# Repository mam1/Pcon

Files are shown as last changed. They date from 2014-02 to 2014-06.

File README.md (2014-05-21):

###Pcon - multi channel programmable controller
- - - - - - - - - 
#####Tag v0.1-e is the currnet production code, it has been running for six months in 2 instalations. The fsmtng branch is the active development branch.  It is under construction and is not stable.
- - - - - - - - -
The state of up to 8 channels can be controlled by time of day, time of day and a sensor value or manually. Each channel has it onwn schedules.  There can be different schedules for each day of the week. The user interface is a serial terminal command line, the command processor fuctions are detailed below. 

The code was developed in c using SimpleIDE. The development platform is a Parallax C3 making use of flash memory and the SD card.  A DS3231 real time clock module is connected to the C3's i2c bus (pins 28,29) to provide a time reference. The DS3231 module, the AQY212GH relays and terminals for the external connections are mounted on an additional board connected to the C3.

The application can be configured to drive 1 to 8 channels using the preprocessor variable *_NUMBER_OF_CHANNELS* in Pcon.h.  It can be configured to drive IO pins or to drive the Parallax Digital IO Board serial interface. The the preprocessor variable *_DRIVEN* in Pcon.h controls which interface is used. In one implementation I am driving AQY212GH PhotoMOS relays connected to 5 propeller IO pins.  The PhotoMOS relays are rated at 60 V AC/DC 1.1 A. These relays come in a 4-pin DIP package.  They work great to control 24 V zone valves. The second instance is driving a Parallax Digital IO board which can control 8, 120 VAC 8 A loads and accept input from 8 sensors. 
####Language:
C - Propgcc, SimpleIDE, Sublime Text
####Hardware:
* C3 micro controller, Parallax  
* Digital IO Board (DIOB), Sharp solid state relays part# S202S02F, Parallax 
* ChronoDot real time clock module, based on a DS3231, adafruit 
* AQY212GH PhotoMOS relays, Newark
* MID400 AC Line Monitor, Newark 

####Command processor functions:
* name channels  
* manually control channel state  
* set channel control mode (manual, time, time & sensor)
* zero on time time for a channel
* load/save channel information to SD card  
* create and maintain schedules for each channel
* copy and paste schedules between days across channels
* load/save schedules to SD card (default file names)
* load/save schedules to a named file on the SD card
* display current time and date
* set date and time
* display schedules
* display system configuration information
* stop and start the control cogs
* set the real time clock
* reboot from EEPROM

####Command processor commands:
######schedule mode commands:
&nbsp;&nbsp;&nbsp;&nbsp;&nbsp;&nbsp;**copy** - copy the schedule for a channel and day to a buffer<br />
&nbsp;&nbsp;&nbsp;&nbsp;&nbsp;&nbsp;**paste** - paste the buffered schedule into a channel and day<br />
&nbsp;&nbsp;&nbsp;&nbsp;&nbsp;&nbsp;**delete** - delete the schedule for the channel and day<br />
&nbsp;&nbsp;&nbsp;&nbsp;&nbsp;&nbsp;**save** - save edited schedules data to default file<br />
&nbsp;&nbsp;&nbsp;&nbsp;&nbsp;&nbsp;**load** - load schedules from default file<br />
&nbsp;&nbsp;&nbsp;&nbsp;&nbsp;&nbsp;**file {file name} {load|save}** - save or load a named schedule file<br />
&nbsp;&nbsp;&nbsp;&nbsp;&nbsp;&nbsp;**edit** - edit the schedule for a specific channel and day<br />
&nbsp;&nbsp;&nbsp;&nbsp;&nbsp;&nbsp;&nbsp;&nbsp;&nbsp;&nbsp;&nbsp;&nbsp;&nbsp;&nbsp;&nbsp;&nbsp;**delete** - delete a schedule record for the specified time<br />
&nbsp;&nbsp;&nbsp;&nbsp;&nbsp;&nbsp;&nbsp;&nbsp;&nbsp;&nbsp;&nbsp;&nbsp;&nbsp;&nbsp;&nbsp;&nbsp;**on** - set the schedule state to on for the specified time<br />
&nbsp;&nbsp;&nbsp;&nbsp;&nbsp;&nbsp;&nbsp;&nbsp;&nbsp;&nbsp;&nbsp;&nbsp;&nbsp;&nbsp;&nbsp;&nbsp;**off** - set the schedule state to off for the specified time<br />
&nbsp;&nbsp;&nbsp;&nbsp;&nbsp;&nbsp;&nbsp;&nbsp;&nbsp;&nbsp;&nbsp;&nbsp;&nbsp;&nbsp;&nbsp;&nbsp;**quit** - exit schedule edit mode<br />           
######channel mode commands:
&nbsp;&nbsp;&nbsp;&nbsp;&nbsp;&nbsp;**save** - save current channel data to default file<br />
&nbsp;&nbsp;&nbsp;&nbsp;&nbsp;&nbsp;**load** - load channel data from default file<br />
&nbsp;&nbsp;&nbsp;&nbsp;&nbsp;&nbsp;**name** - set the name of a channel<br />
&nbsp;&nbsp;&nbsp;&nbsp;&nbsp;&nbsp;**mode** - set the control mode of a channel, 0-manual, 1-time, 2-time & sensor<br />
&nbsp;&nbsp;&nbsp;&nbsp;&nbsp;&nbsp;**zero {channel #}** - set the on time accumlator for a channel to 0<br />
&nbsp;&nbsp;&nbsp;&nbsp;&nbsp;&nbsp;**on {channel #}** - force the control mode of a channel to manual and set the state to on<br />
&nbsp;&nbsp;&nbsp;&nbsp;&nbsp;&nbsp;**off {channel #}** - force the control mode of a channel to manual and set the state to off<br />
######system commands:
&nbsp;&nbsp;&nbsp;&nbsp;&nbsp;&nbsp;**system** - display system information<br />
&nbsp;&nbsp;&nbsp;&nbsp;&nbsp;&nbsp;**status** - display a formated dump of schedules, channel information and current state for all channels for all days<br />
&nbsp;&nbsp;&nbsp;&nbsp;&nbsp;&nbsp;**time** - display current time and date<br />
&nbsp;&nbsp;&nbsp;&nbsp;&nbsp;&nbsp;**set {YYYY}{MM}{DD}{N(day #)}{HH}{MM}{SS}** - set the real time clock<br />
&nbsp;&nbsp;&nbsp;&nbsp;&nbsp;&nbsp;**shutdown** - force all channels to manual control and turn them off, stop control cogs<br />
&nbsp;&nbsp;&nbsp;&nbsp;&nbsp;&nbsp;**start** - start control cogs<br />
&nbsp;&nbsp;&nbsp;&nbsp;&nbsp;&nbsp;**reboot** - reboot the system from EEPROM<br />
&nbsp;&nbsp;&nbsp;&nbsp;&nbsp;&nbsp;**help(?)** - display list of valid commands<br />

Because the command processor is implemented by a state machine there is a lot of flexibility in the way tokens can be entered.  Entering a '?' will display the current state of the command fsm and a list of commands and tokens (INT for a integer and STR for a quoted string) that are valid in that state. ESC will clear input buffers and reset the state machines.   Tokens can be entered individually or strung together. Spaces, commas, colons and slashes will work as a delimiters. If the fsm requires additional information a prompt will be displayed, however the main loop will not wait for input.

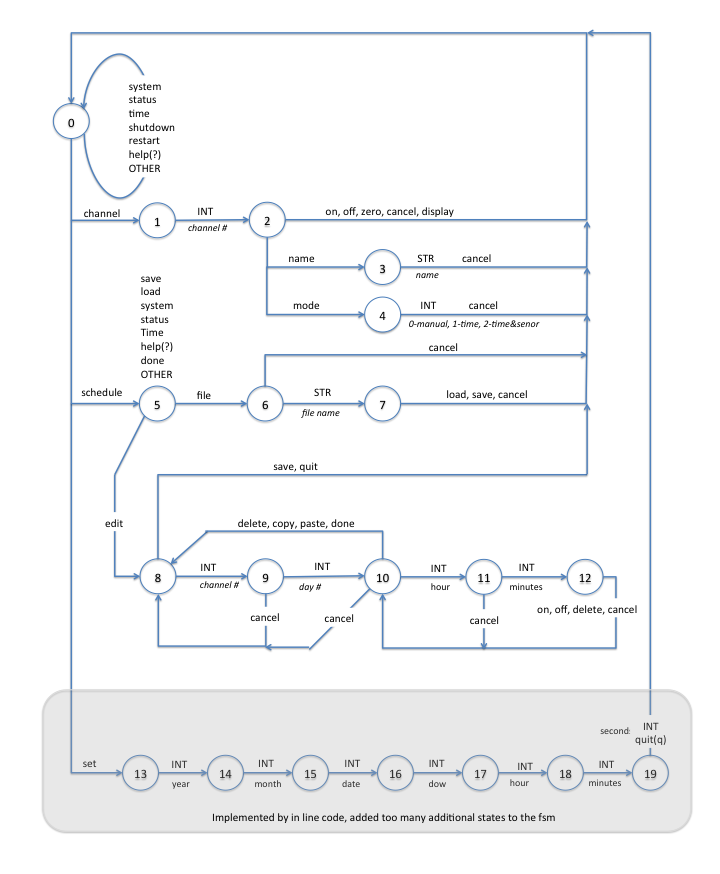
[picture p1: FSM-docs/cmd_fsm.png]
Command Processor FSM


####Schedules:
A schedule is a list of times and corresponding states.  A channel that is controlled by time will be a list of times and states.  For example, a schedule of:

* 1:00  on
* 13:00 off

will result in the channel turning on at 1:00AM and off at 1:00PM.  If the current time is between 13:00 and 24:00 or between 0:0 and 13:00 the channel will be off.  Between 1:00 and 13:00 it will be on. While a schedule of:

* 1:00  off
* 13:00 on 

will result in the channel being off between 1:00 - 13:00. It will be on at any time before 1:00 or after 13:00.

* 1:00  on
* 13:00 off
* 18:00 on

will result in the channel turning on at 1:00, off at 13:00 and on at 18:00.  If the current time is between 1:00 and 13:00 the channel will be on, between 13:00 and 18:00 it will be off, between 18:00 and 0:0 it will be on and between 0:0 and 13:00 it will also be on. 

The maximum number of records for a schedule is configured by setting the preprocessor variable *_MAX_SCHEDULE_RECS*.  Schedules are stored on the SD card. 

####Architecture:
A schedule is a vector of 32 bit unsigned integers. The length is configured by the preprocessor variable *_MAX_SCHEDULE_RECS* .  These are fixed length vectors. I have an alternate implementation using linked lists but his approach is much simpler and has less chance of memory leaks. Since I am already using xmmc size is not a big deal.

The first 32 bits of the vector contain the number of active records in the schedule. The following 32 bit "records" are interpreted as:

* bit 31 (high bit) .... state (0=off, 1=on)
* bit 30-16 ............ key (number of minutes past midnight, 0-1440)
* bit 15-0 ............. sensor value (0-65536)

The schedules for each (day,channel) tuple are combined into one contiguous vector of unsigned integers. The schedule for a particular tuple is accessed via pointer offsets. 

The control part of the application uses 2 cogs, "rtc.cogc" and "dio.cogc".  The rtc cog talks to the DS3231, converts BCD to decimal and updates a time/date buffer in hub memory.  The rtc cog contains i2c bit banging code; first - because the DS3231 requires clock stretching if the code is running in a cog and  second - the library i2c routines are too large. I discovered the need for clock stretching  by developing the bit banging code on the xmmc cog, have it running fine, moving it to a cog and it dies.  It must be the difference in execution speed.  Once I implemented the complete i2c spec (add clock stretching) it runs fine on a cog.  The library i2c routines do not support clock stretching, but that is not important as they are too large to run from a cog.

The dio cog reads the time from the buffer in hub memory.  Once a minute the dio cog creates a control byte.  Each bit controls the state of the corresponding channel. The bits are set based on the current time, the schedule for the channel and the control information for the channel. The dio cog can be forced to update by use of a flag in hub memory. The control byte is sent to either the Parallax Digital IO Board or the PhotoMos relays depending on the application configuration.

The schedule and control information are stored on a SD card and loaded into hub memory at initialization or on command.  

The complex part of the application is the command processor.  XMMC is required because of the code size.  It uses a finite state machine (fsm) to parse the input character stream into tokens and a second fsm to process the tokens.  This type of command processor is probably inappropriate for a micro controller, however no one is paying me anymore so I can do what I want. 

The command processor loops checking to see if a character has been typed. Input buffering has been disabled so the read is non blocking.

**If a character is present**, unless it is an ESC, it is passed to the first state machine (char_fsm). An ESC will clear all buffers and reset both state machines.  The first fsm, char_fsm parses the input stream into tokens and pushes them on to FIFO stack.  A CR will cause char_fsm to pass the stack of tokes to the command processor.  The command processor pops tokens off the stack and feeds them to a second fsm, cmd_fsm until the stack is empty. Then the command processor lets the cms_fsm know there is no more input then continues the main loop.  While cmd_fsm is processing a token stack the main loop is waiting, however, the the control cogs are running independently and are not affected.  They continue to control the channels based the the real time. 
**If a character is not found** the code checks to see if the the cogs have sent any messages.  If the dio cog changes the state of a channel it sets a flag to let the main loop know to update the channel info stored on disk.
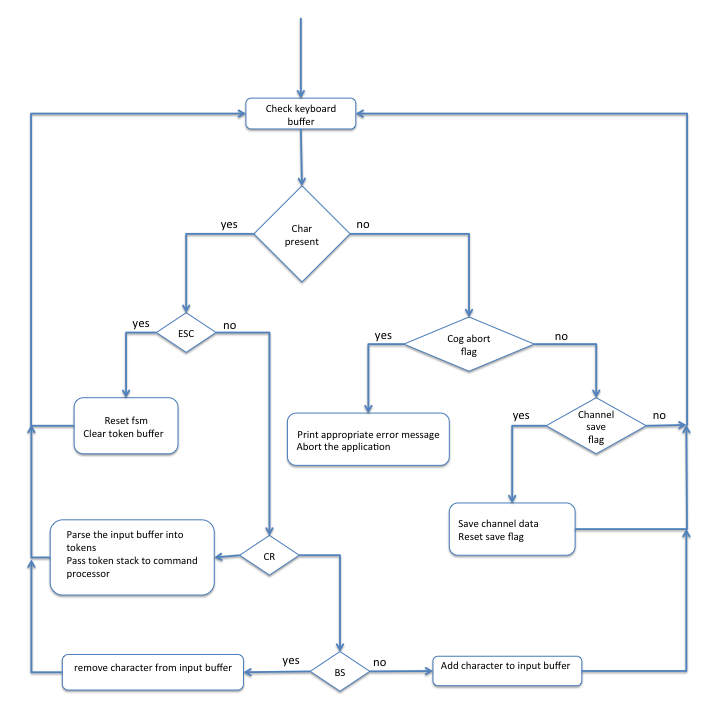
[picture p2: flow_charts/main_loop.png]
Main Event Loop

####SD Files:
Schedules and persistent channel information (name, control mode, state) are stored in files on a SD card. The files are loaded when the code is initialized or reset. They can also be loaded or saved on command.  The files are alway closed after use so the SD card can be replaced to make copies or change behavior.  The file names are generated using the following preprocessor variables:

    #define _FILE_SET_ID            "NNN"
    #define _F_PREFIX               "SSS"
    #define _F_SCHEDULE_SUFIX       ".sch"
    #define _F_CHANNEL_SUFIX        ".ch"

In the following format:

    channel information <SSS><NNN>.ch
    schedules           <SSS><NNN>.sch

####Propeller Pins:

    0 - day light savings on
    1 - AC line power monitor MID400
    2

        3 - 
        4 - dio, DIN
        4 - dio, DATA_RLY
        5 - dio, SCLK_IN
        5 - dio, SCLK_RLY
        6 - dio, LOAD_IN
        7 - dio, LAT_RLY

        3 - 
        4 - dio, DIN
        4 - dio, DATA_RLY
        5 - dio, SCLK_IN
        5 - dio, SCLK_RLY
        6 - dio, LOAD_IN
        7 - dio, LAT_RLY

    8 - SPI
    9 - SPI, SPI_MOSI
    10 - SPI, SPI_MISO
    11 - SPI, SPI_CLK
    12 - composite video
    13 - composite video
    14 - composite video
    15 - toggle Port B header
    16-23 - VGA 
    24 - audio PWM
    25 - SPI
    26 - PS/2_DATA
    27 - PS/2_CLOCK. 
    28 - i2c
    29 - i2c
    30 - USB
    31 - USB

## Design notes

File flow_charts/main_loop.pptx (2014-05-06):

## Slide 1

Reset fsm
Clear token buffer

Check keyboard buffer

Char present

yes

no

yes

ESC

no

yes

Cog abort flag

no

Print appropriate error message
Abort the application

yes

Channel save flag

no

Parse the input buffer into tokens
Pass token stack to command processor

CR

Save channel data
Reset save flag

remove character from input buffer

yes

BS

no

Add character to input buffer

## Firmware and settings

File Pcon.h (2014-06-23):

#ifndef PCON_H_
#define PCON_H_

#define _major_version 1
#define _minor_version 1

#define _FILE_SET_ID            "007"

/* configuration options */
#define _DIOB       1       //configure to drive Parallax Digital IO Board
#define _212GH      2       //configure to drive 5 AYQ212GH relays

#define _DRIVEN     _DIOB

/* propeller io pin assignments */
#if _DRIVEN == _DIOB
    /* if configured to drive the Parallax Digital IO board */
    #define _DataIO          4              // DIO -DIN & DATA_RLY
    #define _Clock           5              // DIO SCLK_IN & SCLK_RLY
    #define _HC165           6              // DIO LOAD_IN Pin
    #define _HC595           7              // DIO LAT_RLY Pin
#else
    /* if configure to drie AYQ212GH relays */
    #define _RLY1           3              // relay 1
    #define _RLY2           4              // relay 2
    #define _RLY3           5              // relay 3
    #define _RLY4           6              // relay 4
    #define _RLY5           7              // relay 5
#endif
#define _toggle_VGA     15              // toggle the port B header to VGA
#define _VGA_start      16              // VGA uses pins 16-
#define _data_pin       26              // keyboard */
#define _clk_pin        27              // keyboard */
#define _rtcClockPin    28              //i2c - DS3231 clock
#define _rtcDataPin     29              //i2c - DS3231 data

/* cog parameters */
#define _STACK_SIZE_RTC     64
#define _STACK_SIZE_DIO     128

/* character parser fsm */
#define _CHAR_TOKENS     8
#define _CHAR_STATES     4

/* command parser fsm */
#define _CMD_TOKENS     29
#define _CMD_STATES     14 

/* channel parameters */
#if _DRIVEN == _DIOB
    #define _NUMBER_OF_CHANNELS 8 
#else
    #define _NUMBER_OF_CHANNELS 5
#endif
#define _CHANNEL_NAME_SIZE          20
#define _CHANNEL_NAME_BUFFER_SIZE   30
#define _CHANNEL_FILE_NAME_SIZE     30

/* sd card file parameters */
#if _DRIVEN == _DIOB
    #define _F_PREFIX           "dio"
#else
    #define _F_PREFIX           "rly"
#endif

#define _F_SCHEDULE_SUFIX       ".sch"
#define _F_CHANNEL_SUFIX        ".ch"

/* schedule parameters */
#define _DAYS_PER_WEEK          7
#define _MAX_SCHEDULE_RECS      10
#define _SCHEDULE_NAME_SIZE     40
#define _STATE_MASK             B32(10000000,00000000,00000000,00000000)                 
#define _KEY_MASK               B32(01111111,11111111,11111111,11111111) 
#define _BYTES_PER_CHANNEL      (_MAX_SCHEDULE_RECS + 1) * 4
#define _BYTES_PER_DAY          _BYTES_PER_CHANNEL * _NUMBER_OF_CHANNELS

/* buffers */
#define _INPUT_BUFFER           128
#define _TIME_STRING_BUFFER     40
#define _TOKEN_BUFFER           128
#define _VCMD_BUFFER            128
#define _PROMPT_BUFFER          400
#define _SCHEDULE_BUFFER        (_BYTES_PER_DAY * _DAYS_PER_WEEK)/4

/* key codes */
#define _ESC        27
#define _SPACE      32
#define _COLON      58
#define _SLASH      47
#define _COMMA      44
#define _BS         8
#define _QUOTE      34
#define _CR         13
#define _NO_CHAR    255

/* reboot system */
#define reboot() __builtin_propeller_clkset(0x80)

/****************** functions *****************/
void disp_sys(void);

/*******************/
/* data structures */
/*******************/

/* action routines for the cmd fsm */
typedef int(*CMD_ACTION_PTR)(int, int *,char *); 

/* channel control record (ccr) */
typedef struct  
{
    int                 c_mode; //Control mode: 0-manual, 1-time, 2-time & sensor
    int                 state;  //Channel State: 0-off, 1-on
    char                name[_CHANNEL_NAME_SIZE];
    int                 time_on; // accumulated minutes of on time for channel
}CCR;

/* time/date buffer */
typedef struct{
    uint8_t     sec;
    uint8_t     min;
    uint8_t     hour;
    uint8_t     day;
    uint8_t     month;
    uint8_t     year;
    uint8_t     dow;
}TD_BUF;

/* rtc cog control block */
typedef volatile struct 
{
    int                 tdb_lock;   //lock ID for time date buffer
    int                 abt;        //!= 0 cog requests a system abort,value = error code
    int                 update;     //trigger update flag, 1=wait, 0=update 
    TD_BUF              td_buffer;  //time, date & dow stored as uint8_t 
}RTC_CB;
 
/*  data structures for indexing the schedule array */
typedef struct
 {
    uint32_t            rec[_MAX_SCHEDULE_RECS+1];
 } SCH;

typedef struct
 {
    SCH                 sch[_NUMBER_OF_CHANNELS];
 } DAY;


/* dio cog control block */
typedef volatile struct 
{
    int        tdb_lock;    //lock ID for time date buffer
    int        cca_lock;    //lock ID for the channel control array
    int        sch_lock;    //lock ID for schedule records
    int        abt;         //!= 0 cog requests a system abort,value = error code
    int        *update_ptr; //pointer to trigger update flag, 1=wait, 0=update 
    TD_BUF     *td_ptr;     //pointer to the time date buffer
    uint32_t   *sch_ptr;    //schedule buffer pointer
    CCR        cca[_NUMBER_OF_CHANNELS];                 //channel control array
    int        save_cca;     //!= 0 cog request a save of the channel data

}DIO_CB;
#endif

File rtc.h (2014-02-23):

/**************************************/
/*  rtc.h -                           */
/*  header file for rtc.cogc          */ 
/**************************************/

#ifndef _RTC_H_
#define _RTC_H_

/* set i2c high by allowing the pin to float high, set low by forcing it low */
#define i2c_float_scl_high  DIRA &= ~(1<<scl)
#define i2c_set_scl_low     DIRA |= (1<<scl)
#define i2c_float_sda_high  DIRA &= ~(1<<sda)
#define i2c_set_sda_low     DIRA |= (1<<sda)

/*  DS3231 stuff */
#define DS3231_Address              0x68                                                              
#define DS3231_Read_addr            ((DS3231_Address << 1) | 0x01) 
#define DS3231_Write_addr           ((DS3231_Address << 1) & 0xFE)
#define ACK                         0
#define NACK                        1
    
#endif // _RTC_H_

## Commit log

2014-02-27 added support for AQY212GH relays
2014-03-12 insert and add schedule working
2014-03-13 Contents of Master replaced with OneRead
    [Pcon.h]
2014-04-11 track .gitconfig
2014-04-26 add board layouts
    [C3_daughter_board.fzz, ups.fzz]
2014-05-04 new fsm inserted in README
2014-05-05 add flow chart for mail loop
2014-05-05 link flow chart picture
2014-05-05 add command to reset the dio board
2014-06-23 working on mid400 board
2014-06-23 code size problem? breakes when I increase the size of edit schedule buffers
    [Pcon.h]
2014-06-23 adding the MID400 board layout
    [MID400.fzz, channel.fzz]
2014-06-24 mid400 board
    [MID400.fzz]
2014-06-28 mid400 board layout
    [MID400.fzz]
2014-07-06 working on ups board
    [ups.fzz]
2014-07-06 board design
    [MID400.fzz, ups.fzz]
2014-07-06 ups board design
    [ups.fzz]
